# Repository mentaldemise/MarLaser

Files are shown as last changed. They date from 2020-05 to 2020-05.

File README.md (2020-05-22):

https://github.com/adam-p/markdown-here/wiki/Markdown-Cheatsheet#hr

# Making the K40 not suck, a simple plan.

## WARNINGS:
1. This is not going to go into modifying a RAMPS board to support 24V. 
   * If you're brave enough to try this, then use this [link](https://github.com/ExplodingLemur/presentations/wiki/K40-RAMPS-Conversion) to follow his instructions on modifying the board
2. An ability to either solder or spare cash to purchase parts.

# Baseline

This is a Marlin 2.0 build with all the normal laser options set. This is the same firmware configuration that's used in the top "Result" video. The switch from this to that was Lightburn adding support for Inline mode. A Regular Expression can be run on existing Lightburn output as follows:

* Export your gcode for Marlin to desktop. Open it in Notepad++ then:
  * replace all M03 with “I”
  * replace ^(I.+)[\n](G1.+)$ with $2 $1

^This is very much at your own peril. It works for me. I don't mind breaking my stuff.

<a href="https://www.youtube.com/watch?feature=player_embedded&v=LqSpBpukYX4" target="_blank">
IMAGE ALT TEXT HERE
</a>

# Results for just ramps, no stepper upgrade:
<a href="https://www.youtube.com/watch?feature=player_embedded&v=vAA65vcwuIo" target="_blank">
IMAGE ALT TEXT HERE
</a>

## Materials:

### Note on Materials: The initial write-up here is going to be just for RAMPS, then I'm going to add the stuff for my enclosure for exhaust/cooling/air assist, and then come back and add an addendum for using the LPC1768 board for Raster.

* RAMPS 1.4(Trigorilla or other **24V friendly**) *** MKS Board Sgen L V1
* K40 Breakout or skills 
  * https://oshpark.com/shared_projects/3W1BpcNl 
  * $15USD at https://awesome.tech/product/k40-middlemen-board/
  * BRD and SCH files included below for slim version
  * Connector part is linked from [this](https://github.com/ExplodingLemur/presentations/wiki/K40-RAMPS-Conversion) site, search for "connector for the cable"
* 4 Relay board **
* 5V laser diode **
* 3D Printer
* 24V PSU(Or run relay?) **
* 2A stepper for X(At least)

---
Goal: Make K40 not suck.

Inspiration/Source: http://3dprintzothar.blogspot.com/2014/08/40-watt-chinese-co2-laser-upgrade-with.html

## Breakout wiring
#### Note the Buck converter in this picture is used for something else later on.
These are difficult to see, but on my home-made K40 breakout we have:

|Wire Color| Purpose| Pin|
|---|---|---|
|Red| 5V on RAMPS| Any available 5V|
|Black| GND on Ramps| Any available GND|
|4 Pin Dupont| X stepper|X motor|
|White| X Endstop| X- Signal|
|Grey| Y Endstop| Y- Signal|



Use this link to download the Eagle BRD file [Board File](media/k40_breakout/K40_MiddleMan_002A.brd)  
Use this link to download the Eagle SCH file [Board Schematic](media/k40_beakout/K40_MiddleMan_002A.sch)

## Board mount
I used [This thing](https://www.thingiverse.com/thing:2155376) to mount the Trigorilla board in my case. You can find others that will work for whatever RAMPS variant you have. The inpiration link above I think has one for a regule RAMPS even.



## Wiring RAMPS to Laser PSU
PSU Wiring:
#### Note that you may need to check the pinout on your PSU
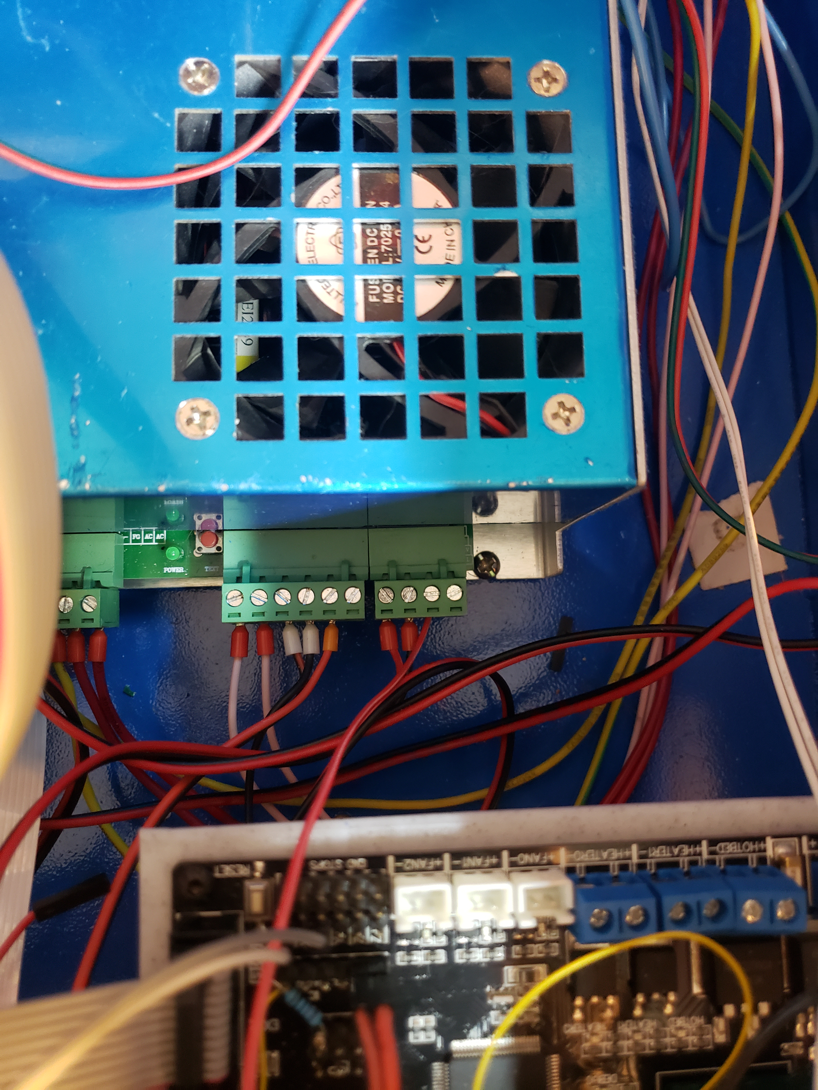
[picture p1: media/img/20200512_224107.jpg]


Top connector(top to bottom)
* NC
* 5V going to any open 5V pin on RAMPS
* GND going to - of 5A input on RAMPS
* +24V going to + of 5A input on RAMPS
---
Bottom Connector(top to bottom)
* NC
* Laser PWM - 6 -- There are only certain pins this can go on because of timers. Leave it on 6 to be safe.
* GND going to any open - on RAMPS
* Laser Enable/Fire - 5 - This is just a digital IO so you can use whichever you want - 10K resistor to +5V here to stop sporadic turnon during boot if interlock is off
* One side of enable push-button toggle
* Other side of enable push-button toggle
---

## Step Calibration
An important part of getting Marlin right on your machine is making sure that distances are correct. If you move 20MM in X when you thought you were going 19MM then there's a bit problem.

This LightBurn file can be used to calibrate steps. There's a 20mmX20mm square with 5mm intervals and axis labels. Cut the outside and etch the inside, measure, and adjust until you get 20x20 with a caliper. Then cut the two triangles(one is rotated 90 degrees), if the two triangles stack up the same then your steps are at least correctly proportioned. 

Use this link to download the Calibration file [Calibration File](media/calibration/20mmSquareStepCal.lbrn)  

~~### 12V buck for Relays
Stepping 24V down to 5V to run switches and the relay coils~~

### Relay board
Runs: Cooling(water pump), Exhaust, and Air Assist via panel buttons

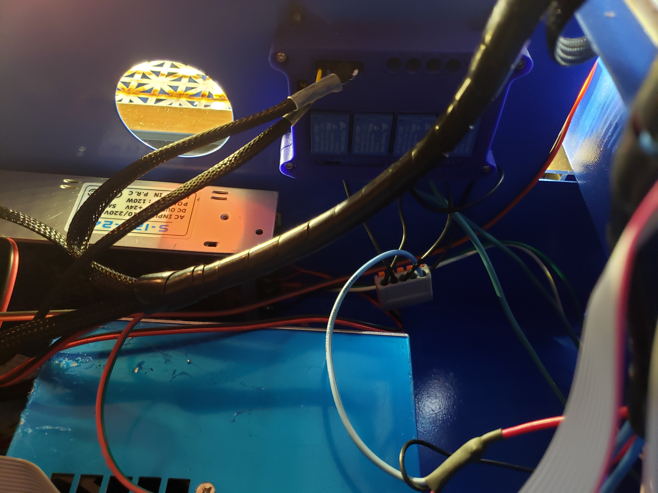
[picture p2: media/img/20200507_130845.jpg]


### Panel

Here's the new panel I have hooked up. The relay board will better explain, but the push buttons are feeding power to a relay in all cases but the aiming diode.

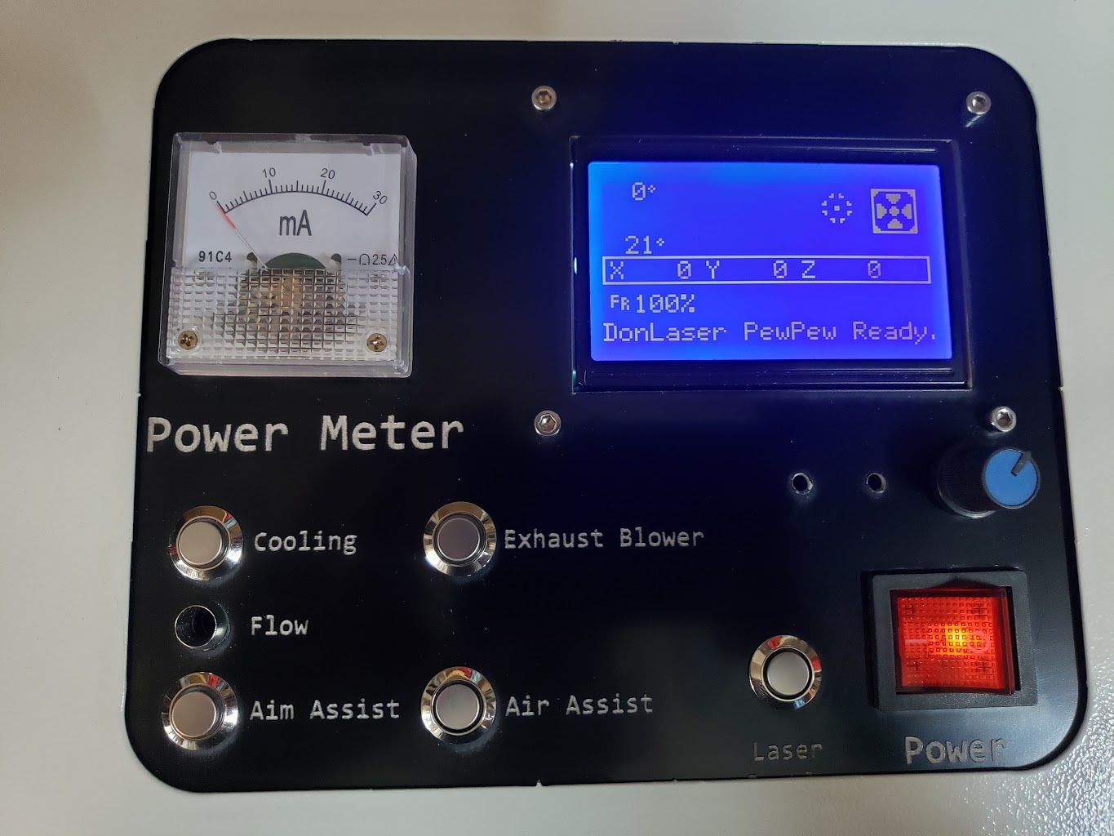
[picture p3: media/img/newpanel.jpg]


Here is the [DXF File](media/panel_files/NewPanel.dxf)
Here is the [LBRN File](media/panel_files/LaserPanel.lbrn)

## Water pump/flow indicator?

*** When hooking up the chiller and cutting my speed/power for MDF went from 10/32 to barely get through to 10/28.

This setup works just fine without the chiller in the loop for the K40 if you turn your pump off between using the laser. I found after a few hours the pump alone would heat the water up(only having 5Gallons doesn't help)

We have an aquarium pump in the bottom of a 5 gallon bucket.  
Outlet on it goes to the IN side of a chiller.  
Outlet of the chiller goes to the IN side of a 12V generator.   
Outlet of the generator then goes to the laser in.

Generator output then goes to the "FLOW" led on the panel. This needs some revision yet.  
There's a Thermistor stuck to the side of the bucket the pump is in and hooked up to TH0 on the RAMPS board to get water temp on the screen as well.

Water pump is controlled via one of the panel buttons and a relay using one of the original outlets on the back of the case(with wiring corrected)

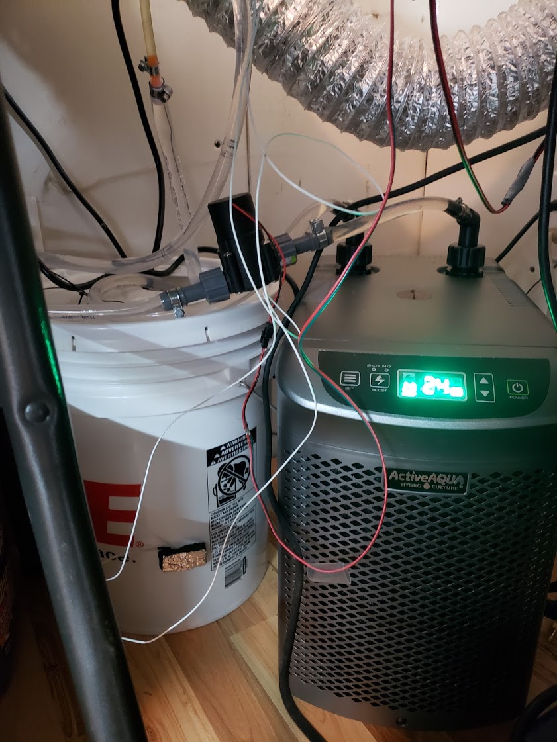
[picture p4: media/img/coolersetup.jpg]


**wire cleanup will come when I get my panel mount connectors this coming week.

## MKS Upgrade for Raster
---
<a href="https://www.youtube.com/watch?feature=player_embedded&v=EFzJmyRZ6YY" target="_blank">
IMAGE ALT TEXT HERE
</a>
---
<a href="https://www.youtube.com/watch?feature=player_embedded&v=5UWSP2m-0Rs" target="_blank">
IMAGE ALT TEXT HERE
</a>

Case was printed using [This thing](https://www.thingiverse.com/thing:4174973) and [this cooling duct](https://www.thingiverse.com/thing:4191051).

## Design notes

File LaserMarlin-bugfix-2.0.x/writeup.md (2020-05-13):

https://github.com/adam-p/markdown-here/wiki/Markdown-Cheatsheet#hr

# Making the K40 not suck, a simple plan.

## Materials:
* RAMPS 1.4(Trigorilla or other 24V friendly preferred) ** MKS Board
* K40 Breakout or skills 
  * https://oshpark.com/shared_projects/3W1BpcNl 
  * $15USD at https://awesome.tech/product/k40-middlemen-board/
* 4 Relay board
* 5V laser diode
* 3D Printer
* 24V PSU(Or run relay?)
* 2A stepper for X(At least)

---
Goal: Make K40 not suck.

Inspiration/Source: http://3dprintzothar.blogspot.com/2014/08/40-watt-chinese-co2-laser-upgrade-with.html

### Breakout wiring

### 12V buck for Relays

### Relay board

### Panel

### Board mount

### Water pump/flow indicator?

## MKS Upgrade for Raster

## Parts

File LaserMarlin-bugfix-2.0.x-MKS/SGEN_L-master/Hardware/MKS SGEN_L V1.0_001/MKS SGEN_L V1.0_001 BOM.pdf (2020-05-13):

Designator | Comment | Footprint | Quantity
AUX-1 | Header 4X2 | DC8P | 1
C1 | 12pF | C0603 | 1
C2 | 12pF | C0603 | 1
C3 | 10uF | C0805 | 1
C4 | 0.1uF | C0603 | 1
C6 | 0.1uF | C0603 | 1
C7 | 0.1uF | C0603 | 1
C8 | 0.1uF | C0603 | 1
C9 | 0.1uF | C0603 | 1
C10 | 0.1uF | C0603 | 1
C11 | 0.1uF | C0603 | 1
C12 | 0.1uF | C0603 | 1
C13 | 100uF | RVT | 1
C14 | 100uF | RVT | 1
C15 | 0.1uF | C0603 | 1
C16 | 0.1uF | C0603 | 1
C17 | 220uF | RVT | 1
C18 | 100uF | RVT | 1
C19 | 0.1uF | C0603 | 1
C20 | 150pF | C0603 | 1
C21 | 10uF | C0805 | 1
C22 | 10uF | C0805 | 1
C23 | 0.1uF | C0603 | 1
C24 | 0.1uF | C0603 | 1
C25 | 0.1uF | C0603 | 1
C26 | 0.1uF | C0603 | 1
C27 | 0.1uF | C0603 | 1
C28 | 0.1uF | C0603 | 1
C29 | 10uF | C0805 | 1
C30 | 10uF | C0805 | 1
C31 | 10uF | C0805 | 1
C32 | 0.1uF | C0603 | 1
C33 | 18pF | C0603 | 1
C34 | 18pF | C0603 | 1
C35 | 0.1uF | C0603 | 1
Cm1_M1 | 100uF | RVT | 1
Cm1_M2 | 100uF | RVT | 1
Cm1_M3 | 100uF | RVT | 1
Cm1_M4 | 100uF | RVT | 1
Cm1_M5 | 100uF | RVT | 1
D1 | LED | LED0603 | 1
D2 | LED | LED0603 | 1
D3 | LED | LED0603 | 1
D4 | LED | LED0603 | 1
D5 | S1G-13-F | D-SMA | 1
D6 | S1A-13-F | D-SMA | 1

D7 | B340A-13-F | D-SMA | 1 D8 | LED | LED0603 | 1 D9 | SS12 | D-SMA | 1 D10 | LED | LED0603 | 1 D11 | LED | LED0603 | 1 D12 | LED | LED0603 | 1 D13 | LED | LED0603 | 1 EXP1 | Header 5X2 | DC10P | 1 EXP2 | Header 5X2 | DC10P | 1 F1 | 30A | F1206 | 1 F2 | 15A | F1206 | 1 F3 | 1A | MF-MSMF050 | 1 F4 | 500mA | MF-MSMF050 | 1 J1 | Header 2 | HDR1X2 | 1 J2 | Header 3X2 | HDR2X3 | 1 J3 | XH-2A | XH-2A | 1 J4 | DG302-4P 5.0 | DG302-5.0-4P | 1 J5 | HG129-2P | HG129-2P | 1 J6 | X- | XH-3A | 1 J7 | X+ | XH-3A | 1 J8 | Y- | XH-3A | 1 J9 | Y+ | XH-3A | 1 J10 | Z- | XH-3A | 1 J11 | Z+ | XH-3A | 1 J12 | Header 5X2 | HDR2X5 | 1 J13 | Header 2 | HDR1X2 | 1 J14 | Header 2 | HDR1X2 | 1 J15 | Header 2 | HDR1X2 | 1 J16 | Header 2 | HDR1X2 | 1 J17 | Header 2 | HDR1X2 | 1 J18 | USB | USBB | 1 J19_M1 | Header 2 | HDR1X2 | 1 J19_M2 | Header 2 | HDR1X2 | 1 J19_M3 | Header 2 | HDR1X2 | 1 J19_M4 | Header 2 | HDR1X2 | 1 J19_M5 | Header 2 | HDR1X2 | 1 J20 | Header 3X2 | HDR2X3 | 1 J21 | XH-2A | XH-2A | 1 J22 | Header 3 | HDR1X3 | 1 Jc1_M1 | Header 4 | HDR1X4 | 1 Jc1_M2 | Header 4 | HDR1X4 | 1 Jc1_M3 | Header 4 | HDR1X4 | 1 Jc1_M4 | Header 4 | HDR1X4 | 1 Jc1_M5 | Header 4 | HDR1X4 | 1 Jm3_M1 | DIP16 | DIP8825 | 1 Jm3_M2 | DIP16 | DIP8825 | 1 Jm3_M3 | DIP16 | DIP8825 | 1

Jm3_M4 | DIP16 | DIP8825 | 1 Jm3_M5 | DIP16 | DIP8825 | 1 Jm4_M1 | Header 4 | HDR1X4 | 1 Jm4_M2 | Header 4 | HDR1X4 | 1 Jm4_M3 | Header 4 | HDR1X4 | 1 Jm4_M4 | Header 4 | HDR1X4 | 1 Jm4_M5 | Header 4 | HDR1X4 | 1 JM1_M1 | Header 4H | XH-4A | 1 JM1_M2 | Header 4H | XH-4A | 1 JM1_M3 | Header 4H | XH-4A | 1 JM1_M4 | Header 4H | XH-4A | 1 JM1_M5 | Header 4H | XH-4A | 1 Jm2_M1 | Header 4X2 | HDR2X4 | 1 Jm2_M2 | Header 4X2 | HDR2X4 | 1 Jm2_M3 | Header 4X2 | HDR2X4 | 1 Jm2_M4 | Header 4X2 | HDR2X4 | 1 Jm2_M5 | Header 4X2 | HDR2X4 | 1 L1 | 15uH/3A | L7*7*4 | 1 LG1 | BLM21 | R0805 | 1 POWER1 | 129-5.08 | 129-5.08 | 1 Q1 | HY1403 | TO-252AA | 1 Q2 | HY1403 | TO-252AA | 1 Q3 | HY1403 | TO-252AA | 1 Q4 | HY3403 | TO-252AA | 1 Q5 | FDN340P | SOT-23 | 1 R1 | 1M | R0603 | 1 R6 | 10K | R0603 | 1 R7 | 10K | R0603 | 1 R8 | 1.8K | R0603 | 1 R9 | 100K | R0603 | 1 R10 | 210k | R0603 | 1 R11 | 40.2k | R0603 | 1 R12 | 24.9k | R0603 | 1 R13 | 100K | R0603 | 1 R14 | 100K | R0603 | 1 R15 | 1K | R0603 | 1 R16 | 1K | R0603 | 1 R17 | 1K | R0603 | 1 R18 | 1K | R0603 | 1 R19 | 1K | R0603 | 1 R20 | 10K | R0603 | 1 R21 | 10K | R0603 | 1 R22 | 10K | R0603 | 1 R23 | 1K | R0603 | 1 R24 | 1K | R0603 | 1 R25 | 1K | R0603 | 1 R26 | 10K | R0603 | 1

R27 | 10K | R0603 | 1 R28 | 10K | R0603 | 1 R29 | 1K | R0603 | 1 R30 | 1K | R0603 | 1 R31 | 1K | R0603 | 1 R32 | 1.5K | R0603 | 1 R33 | 33 | R0603 | 1 R34 | 33 | R0603 | 1 R35 | 33 | R0603 | 1 R37 | 100 | R0603 | 1 R38 | 100 | R0603 | 1 R39 | 10K | R0603 | 1 Rm1_M1 | 10K | R0603 | 1 Rm1_M2 | 10K | R0603 | 1 Rm1_M3 | 10K | R0603 | 1 Rm1_M4 | 10K | R0603 | 1 Rm1_M5 | 10K | R0603 | 1 RPK0 | 1K | RPACK4 | 1 RPK1 | 100 | RPACK4 | 1 RPK2 | 100 | RPACK4 | 1 RPK3 | 100 | RPACK4 | 1 RPK4 | 100 | RPACK4 | 1 RPK5 | 100 | RPACK4 | 1 RPK6 | 100 | RPACK4 | 1 RPK7 | 4.7K | RPACK4 | 1 RPK8 | 100 | RPACK4 | 1 RPK9 | 10K | RPACK4 | 1 RPK10 | 10 | RPACK4 | 1 RPK11 | 100K | RPACK4 | 1 RPK12 | 1.8K | RPACK4 | 1 S1 | TS42 | TS42 | 1 SD | microSD | microSD-2 | 1 TB | Header 2 | XH-2A | 1 TH1 | Header 2 | XH-2A | 1 TH2 | Header 2 | XH-2A | 1 U1 | LPC1768 | LQFP100 | 1 U2 | MP1584 | SOIC8E | 1 U3 | LM1117-3.3V | SOT223-4N | 1 U4 | 74HC125PW | TSSOP-14 | 1 Y1 | 12MHz | CRY5032 | 1 Z1 | CG0603MLC-05E | R0603 | 1 Z2 | CG0603MLC-05E | R0603 | 1 Z3 | CG0603MLC-05E | R0603 | 1

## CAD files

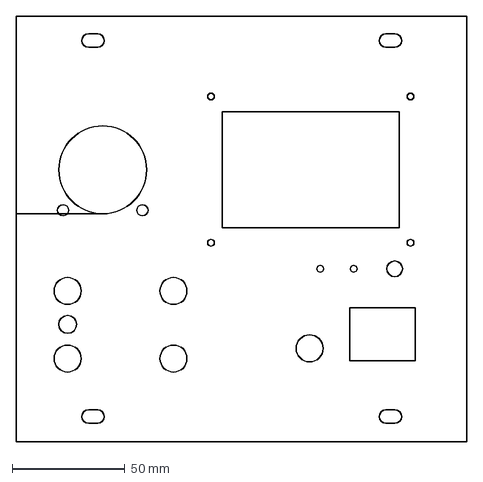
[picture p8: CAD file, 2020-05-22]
media/panel_files/NewPanel.dxf
200.0 x 189.0 mm

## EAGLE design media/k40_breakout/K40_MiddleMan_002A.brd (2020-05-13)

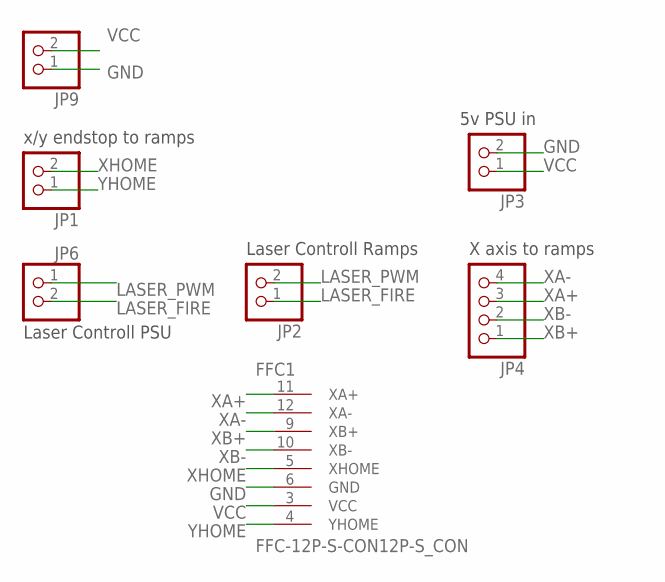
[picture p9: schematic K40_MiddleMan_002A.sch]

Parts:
FFC1: FFC-12P-S-CON12P-S_CON; FFC
JP1, JP2, JP3, JP6, JP9: PINHD-1X2; 1X02
JP4: PINHD-1X4; 1X04

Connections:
GND: FFC1.6 (GND), JP3.2, JP9.1
LASER_FIRE: JP2.1, JP6.2
LASER_PWM: JP2.2, JP6.1
VCC: FFC1.3 (VCC), JP3.1, JP9.2
XA+: FFC1.11 (XA+), JP4.3
XA-: FFC1.12 (XA-), JP4.4
XB+: FFC1.9 (XB+), JP4.1
XB-: FFC1.10 (XB-), JP4.2
XHOME: FFC1.5 (XHOME), JP1.2
YHOME: FFC1.4 (YHOME), JP1.1

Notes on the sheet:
5v PSU in
X axis to ramps
Laser Controll Ramps
Laser Controll PSU
x/y endstop to ramps

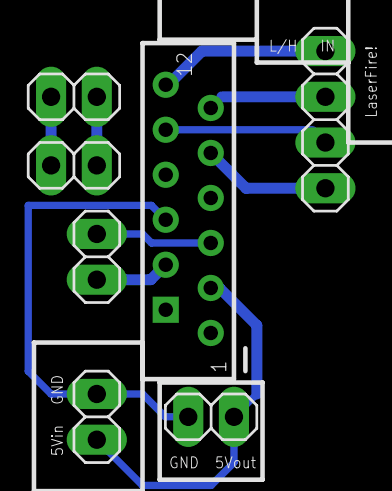
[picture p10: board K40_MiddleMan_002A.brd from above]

Board: 2 copper layers, 7 parts (0 on the bottom side), 10 nets.

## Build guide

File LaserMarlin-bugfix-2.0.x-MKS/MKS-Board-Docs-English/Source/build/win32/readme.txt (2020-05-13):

The bsdtar binaries in this directory were downloaded from http://gnuwin32.sourceforge.net/packages/libarchive.htm
The curl binaries in this directory were downloaded from http://curl.haxx.se/download.html
The md5sum binaries in this directory were downloaded from http://gnuwin32.sourceforge.net/packages/coreutils.htm
The make binaries in this directory were downloaded from http://gnuwin32.sourceforge.net/packages/make.htm

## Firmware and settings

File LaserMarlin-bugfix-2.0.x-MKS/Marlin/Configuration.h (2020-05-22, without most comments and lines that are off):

#pragma once
#define CONFIGURATION_H_VERSION 020005
#define STRING_CONFIG_H_AUTHOR "(DonLaser Pew Pew)" // Who made the changes.
#define SHOW_BOOTSCREEN
#define SERIAL_PORT -1
#define BAUDRATE 250000
  #define MOTHERBOARD BOARD_MKS_SGEN_L
#define CUSTOM_MACHINE_NAME "DonLaser PewPew"
#define EXTRUDERS 1
#define DEFAULT_NOMINAL_FILAMENT_DIA 3.0
#define TEMP_SENSOR_0 1
#define TEMP_SENSOR_1 0
#define TEMP_SENSOR_2 0
#define TEMP_SENSOR_3 0
#define TEMP_SENSOR_4 0
#define TEMP_SENSOR_5 0
#define TEMP_SENSOR_6 0
#define TEMP_SENSOR_7 0
#define TEMP_SENSOR_BED 0
#define TEMP_SENSOR_PROBE 0
#define TEMP_SENSOR_CHAMBER 0
#define DUMMY_THERMISTOR_998_VALUE 25
#define DUMMY_THERMISTOR_999_VALUE 100
#define MAX_REDUNDANT_TEMP_SENSOR_DIFF 10
#define TEMP_RESIDENCY_TIME     10  // (seconds) Time to wait for hotend to "settle" in M109
#define TEMP_WINDOW              1  // (°C) Temperature proximity for the "temperature reached" timer
#define TEMP_HYSTERESIS          3  // (°C) Temperature proximity considered "close enough" to the target
#define TEMP_BED_RESIDENCY_TIME 10  // (seconds) Time to wait for bed to "settle" in M190
#define TEMP_BED_WINDOW          1  // (°C) Temperature proximity for the "temperature reached" timer
#define TEMP_BED_HYSTERESIS      3  // (°C) Temperature proximity considered "close enough" to the target
#define HEATER_0_MINTEMP   5
#define HEATER_1_MINTEMP   5
#define HEATER_2_MINTEMP   5
#define HEATER_3_MINTEMP   5
#define HEATER_4_MINTEMP   5
#define HEATER_5_MINTEMP   5
#define HEATER_6_MINTEMP   5
#define HEATER_7_MINTEMP   5
#define BED_MINTEMP        5
#define HEATER_0_MAXTEMP 275
#define HEATER_1_MAXTEMP 275
#define HEATER_2_MAXTEMP 275
#define HEATER_3_MAXTEMP 275
#define HEATER_4_MAXTEMP 275
#define HEATER_5_MAXTEMP 275
#define HEATER_6_MAXTEMP 275
#define HEATER_7_MAXTEMP 275
#define BED_MAXTEMP      150
#define BANG_MAX 255     // Limits current to nozzle while in bang-bang mode; 255=full current
#define PID_MAX BANG_MAX // Limits current to nozzle while PID is active (see PID_FUNCTIONAL_RANGE below); 255=full current
#define PID_K1 0.95      // Smoothing factor within any PID loop
#define MAX_BED_POWER 255 // limits duty cycle to bed; 255=full current
#define PREVENT_COLD_EXTRUSION
#define EXTRUDE_MINTEMP 170
#define PREVENT_LENGTHY_EXTRUDE
#define EXTRUDE_MAXLENGTH 200
#define USE_XMIN_PLUG
#define USE_YMIN_PLUG
#define USE_ZMIN_PLUG
#define ENDSTOPPULLUPS
#define X_MIN_ENDSTOP_INVERTING false // Set to true to invert the logic of the endstop.
#define Y_MIN_ENDSTOP_INVERTING false // Set to true to invert the logic of the endstop.
#define Z_MIN_ENDSTOP_INVERTING false // Set to true to invert the logic of the endstop.
#define X_MAX_ENDSTOP_INVERTING false // Set to true to invert the logic of the endstop.
#define Y_MAX_ENDSTOP_INVERTING false // Set to true to invert the logic of the endstop.
#define Z_MAX_ENDSTOP_INVERTING false // Set to true to invert the logic of the endstop.
#define Z_MIN_PROBE_ENDSTOP_INVERTING false // Set to true to invert the logic of the probe.
#define X_DRIVER_TYPE  TMC2209
#define Y_DRIVER_TYPE  TMC2209
#define DEFAULT_AXIS_STEPS_PER_UNIT   { 79.25, 79.25, 4000, 500 }
#define DEFAULT_MAX_FEEDRATE          { 3000, 3000, 5, 25 }
#define DEFAULT_MAX_ACCELERATION      { 3000, 3000, 100, 10000 }
#define DEFAULT_ACCELERATION          3000    // X, Y, Z and E acceleration for printing moves
#define DEFAULT_RETRACT_ACCELERATION  3000    // E acceleration for retracts
#define DEFAULT_TRAVEL_ACCELERATION   3000    // X, Y, Z acceleration for travel (non printing) moves
#define CLASSIC_JERK
  #define DEFAULT_XJERK 20.0
  #define DEFAULT_YJERK 20.0
  #define DEFAULT_ZJERK  0.3
  #define LIMITED_JERK_EDITING        // Limit edit via M205 or LCD to DEFAULT_aJERK * 2
    #define MAX_JERK_EDIT_VALUES { 100, 100, 100, 10 } // ...or, set your own edit limits
#define DEFAULT_EJERK    5.0  // May be used by Linear Advance
#define S_CURVE_ACCELERATION
#define Z_MIN_PROBE_USES_Z_MIN_ENDSTOP_PIN
#define NOZZLE_TO_PROBE_OFFSET { 10, 10, 0 }
#define MIN_PROBE_EDGE 10
#define XY_PROBE_SPEED 8000
#define Z_PROBE_SPEED_FAST HOMING_FEEDRATE_Z
#define Z_PROBE_SPEED_SLOW (Z_PROBE_SPEED_FAST / 2)
#define Z_CLEARANCE_DEPLOY_PROBE   10 // Z Clearance for Deploy/Stow
#define Z_CLEARANCE_BETWEEN_PROBES  5 // Z Clearance between probe points
#define Z_CLEARANCE_MULTI_PROBE     5 // Z Clearance between multiple probes
#define Z_PROBE_LOW_POINT          -2 // Farthest distance below the trigger-point to go before stopping
#define Z_PROBE_OFFSET_RANGE_MIN -20
#define Z_PROBE_OFFSET_RANGE_MAX 20
#define X_ENABLE_ON 0
#define Y_ENABLE_ON 0
#define Z_ENABLE_ON 0
#define E_ENABLE_ON 0 // For all extruders
#define DISABLE_X false
#define DISABLE_Y false
#define DISABLE_Z false
#define DISABLE_E false             // For all extruders
#define DISABLE_INACTIVE_EXTRUDER   // Keep only the active extruder enabled
#define INVERT_X_DIR false
#define INVERT_Y_DIR false
#define INVERT_Z_DIR false
#define INVERT_E0_DIR false
#define INVERT_E1_DIR false
#define INVERT_E2_DIR false
#define INVERT_E3_DIR false
#define INVERT_E4_DIR false
#define INVERT_E5_DIR false
#define INVERT_E6_DIR false
#define INVERT_E7_DIR false
#define X_HOME_DIR -1
#define Y_HOME_DIR -1
#define Z_HOME_DIR -1
#define X_BED_SIZE 350
#define Y_BED_SIZE 240
#define X_MIN_POS 0
#define Y_MIN_POS 0
#define Z_MIN_POS 0
#define X_MAX_POS X_BED_SIZE
#define Y_MAX_POS Y_BED_SIZE
#define Z_MAX_POS 200
#define MIN_SOFTWARE_ENDSTOPS
  #define MIN_SOFTWARE_ENDSTOP_X
  #define MIN_SOFTWARE_ENDSTOP_Y
  #define MIN_SOFTWARE_ENDSTOP_Z
#define MAX_SOFTWARE_ENDSTOPS
  #define MAX_SOFTWARE_ENDSTOP_X
  #define MAX_SOFTWARE_ENDSTOP_Y
  #define MAX_SOFTWARE_ENDSTOP_Z
#define HOMING_FEEDRATE_XY (50*60)
#define HOMING_FEEDRATE_Z  (4*60)
#define VALIDATE_HOMING_ENDSTOPS
#define EEPROM_SETTINGS     // Persistent storage with M500 and M501
#define EEPROM_CHITCHAT       // Give feedback on EEPROM commands. Disable to save PROGMEM.
#define EEPROM_BOOT_SILENT    // Keep M503 quiet and only give errors during first load
  #define EEPROM_AUTO_INIT  // Init EEPROM automatically on any errors.
#define DEFAULT_KEEPALIVE_INTERVAL 2  // Number of seconds between "busy" messages. Set with M113.
#define BUSY_WHILE_HEATING            // Some hosts require "busy" messages even during heating
#define PREHEAT_1_LABEL       "PLA"
#define PREHEAT_1_TEMP_HOTEND 180
#define PREHEAT_1_TEMP_BED     70
#define PREHEAT_1_FAN_SPEED     0 // Value from 0 to 255
#define PREHEAT_2_LABEL       "ABS"
#define PREHEAT_2_TEMP_HOTEND 240
#define PREHEAT_2_TEMP_BED    110
#define PREHEAT_2_FAN_SPEED     0 // Value from 0 to 255
#define PRINTJOB_TIMER_AUTOSTART
#define LCD_LANGUAGE en
#define DISPLAY_CHARSET_HD44780 JAPANESE
#define LCD_INFO_SCREEN_STYLE 0
#define INDIVIDUAL_AXIS_HOMING_MENU
#define REPRAP_DISCOUNT_FULL_GRAPHIC_SMART_CONTROLLER
#define SOFT_PWM_SCALE 0
#define SERVO_DELAY { 0 }

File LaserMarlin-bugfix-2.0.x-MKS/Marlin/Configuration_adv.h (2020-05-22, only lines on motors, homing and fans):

#define E0_AUTO_FAN_PIN -1
#define E1_AUTO_FAN_PIN -1
#define E2_AUTO_FAN_PIN -1
#define E3_AUTO_FAN_PIN -1
#define E4_AUTO_FAN_PIN -1
#define E5_AUTO_FAN_PIN -1
#define E6_AUTO_FAN_PIN -1
#define E7_AUTO_FAN_PIN -1
#define CHAMBER_AUTO_FAN_PIN -1
#define HOMING_BUMP_MM      { 5, 5, 2 }       // (mm) Backoff from endstops after first bump
#define HOMING_BUMP_DIVISOR { 2, 2, 4 }       // Re-Bump Speed Divisor (Divides the Homing Feedrate)
#define QUICK_HOME                          // If G28 contains XY do a diagonal move first
#define HOME_AFTER_DEACTIVATE  // Require rehoming after steppers are deactivated
#define MICROSTEP_MODES { 16, 16, 16, 16, 16, 16 } // [1,2,4,8,16]
    #define X_CURRENT       1500        // (mA) RMS current. Multiply by 1.414 for peak current.
    #define X_CURRENT_HOME  X_CURRENT  // (mA) RMS current for sensorless homing
    #define X_MICROSTEPS     16    // 0..256
    #define Y_CURRENT       1300
    #define Y_CURRENT_HOME  Y_CURRENT
    #define Y_MICROSTEPS     16
  #define X_HYBRID_THRESHOLD     100  // [mm/s]
  #define X2_HYBRID_THRESHOLD    100
  #define Y_HYBRID_THRESHOLD     100
  #define Y2_HYBRID_THRESHOLD    100
  #define Z_HYBRID_THRESHOLD       3
  #define Z2_HYBRID_THRESHOLD      3
  #define Z3_HYBRID_THRESHOLD      3
  #define Z4_HYBRID_THRESHOLD      3
  #define E0_HYBRID_THRESHOLD     30
  #define E1_HYBRID_THRESHOLD     30
  #define E2_HYBRID_THRESHOLD     30
  #define E3_HYBRID_THRESHOLD     30
  #define E4_HYBRID_THRESHOLD     30
  #define E5_HYBRID_THRESHOLD     30
  #define E6_HYBRID_THRESHOLD     30
  #define E7_HYBRID_THRESHOLD     30

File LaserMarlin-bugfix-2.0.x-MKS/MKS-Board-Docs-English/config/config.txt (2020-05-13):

# NOTE Lines must not exceed 132 characters
# Robot module configurations : general handling of movement G-codes and slicing into moves
default_feed_rate                            4000             # Default rate ( mm/minute ) for G1/G2/G3 moves
default_seek_rate                            4000             # Default rate ( mm/minute ) for G0 moves
mm_per_arc_segment                           0.5              # Arcs are cut into segments ( lines ), this is the length for
                                                              # these segments.  Smaller values mean more resolution,
                                                              # higher values mean faster computation
mm_per_line_segment                          5                # Lines can be cut into segments ( not usefull with cartesian
                                                              # coordinates robots ).

# Arm solution configuration : Cartesian robot. Translates mm positions into stepper positions
alpha_steps_per_mm                           78.7402               # Steps per mm for alpha stepper
beta_steps_per_mm                            78.7402               # Steps per mm for beta stepper
gamma_steps_per_mm                           400             # Steps per mm for gamma stepper

# Planner module configuration : Look-ahead and acceleration configuration
planner_queue_size                           32               # DO NOT CHANGE THIS UNLESS YOU KNOW EXACTLY WHAT YOU ARE DOING
acceleration                                 600             # Acceleration in mm/second/second.
z_acceleration                              60              # Acceleration for Z only moves in mm/s^2, 0 uses acceleration which is the default. DO NOT SET ON A DELTA
acceleration_ticks_per_second                1000             # Number of times per second the speed is updated
junction_deviation                           0.02             # Similar to the old "max_jerk", in millimeters,
                                                              # see https://github.com/grbl/grbl/blob/master/planner.c
                                                              # and https://github.com/grbl/grbl/wiki/Configuring-Grbl-v0.8
                                                              # Lower values mean being more careful, higher values means being
                                                              # faster and have more jerk
#z_junction_deviation                        0.0              # for Z only moves, -1 uses junction_deviation, zero disables junction_deviation on z moves DO NOT SET ON A DELTA
#minimum_planner_speed                       0.0              # sets the minimum planner speed in mm/sec





# Stepper module configuration
microseconds_per_step_pulse                  1                # Duration of step pulses to stepper drivers, in microseconds
base_stepping_frequency                      100000           # Base frequency for stepping, higher gives smoother movement

# Cartesian axis speed limits
x_axis_max_speed                             10000            # mm/min
y_axis_max_speed                             10000            # mm/min
z_axis_max_speed                             200              # mm/min

# Stepper module pins ( ports, and pin numbers, appending "!" to the number will invert a pin )
alpha_step_pin                               2.0              # Pin for alpha stepper step signal
alpha_dir_pin                                0.5!              # Pin for alpha stepper direction
alpha_en_pin                                 0.4              # Pin for alpha enable pin
alpha_max_rate                               10000.0          # mm/min

beta_step_pin                                2.1              # Pin for beta stepper step signal
beta_dir_pin                                 0.11             # Pin for beta stepper direction
beta_en_pin                                  0.10             # Pin for beta enable
beta_max_rate                                10000.0          # mm/min

gamma_step_pin                               2.2              # Pin for gamma stepper step signal
gamma_dir_pin                                0.20!             # Pin for gamma stepper direction
gamma_en_pin                                 0.19             # Pin for gamma enable
gamma_max_rate                               100.0            # mm/min

# Serial communications configuration ( baud rate default to 9600 if undefined )
uart0.baud_rate                              115200           # Baud rate for the default hardware serial port
second_usb_serial_enable                     true            # This enables a second usb serial port (to have both pronterface
                                                              # and a terminal connected)
#leds_disable                                true             # disable using leds after config loaded
#play_led_disable                            true             # disable the play led
pause_button_enable                          true             # Pause button enable
#pause_button_pin                            2.12             # pause button pin. default is P2.12
#kill_button_enable                           false            # set to true to enable a kill button
#kill_button_pin                              2.12             # kill button pin. default is same as pause button 2.12 (2.11 is another good choice)
#msd_disable                                 false            # disable the MSD (USB SDCARD) when set to true (needs special binary)
#dfu_enable                                  false            # for linux developers, set to true to enable DFU

# Extruder module configuration
extruder.hotend.enable                          true             # Whether to activate the extruder module at all. All configuration is ignored if false
extruder.hotend.steps_per_mm                    90              # Steps per mm for extruder stepper
extruder.hotend.default_feed_rate               600              # Default rate ( mm/minute ) for moves where only the extruder moves
extruder.hotend.acceleration                    500              # Acceleration for the stepper motor, as of 0.6, arbitrary ratio
extruder.hotend.max_speed                       50               # mm/s

extruder.hotend.step_pin                        2.3              # Pin for extruder step signal
extruder.hotend.dir_pin                         0.22!             # Pin for extruder dir signal
extruder.hotend.en_pin                          0.21             # Pin for extruder enable signal

# extruder offset
#extruder.hotend.x_offset                        0                # x offset from origin in mm
#extruder.hotend.y_offset                        0                # y offset from origin in mm
#extruder.hotend.z_offset                        0                # z offset from origin in mm

# firmware retract settings when using G10/G11, these are the defaults if not defined, must be defined for each extruder if not using the defaults
#extruder.hotend.retract_length                  3               # retract length in mm
#extruder.hotend.retract_feedrate                45              # retract feedrate in mm/sec
#extruder.hotend.retract_recover_length          0               # additional length for recover
#extruder.hotend.retract_recover_feedrate        8               # recover feedrate in mm/sec (should be less than retract feedrate)
#extruder.hotend.retract_zlift_length            0               # zlift on retract in mm, 0 disables
#extruder.hotend.retract_zlift_feedrate          6000            # zlift feedrate in mm/min (Note mm/min NOT mm/sec)



# Second extruder module configuration
#extruder.hotend2.enable                          true             # Whether to activate the extruder module at all. All configuration is ignored if false
#extruder.hotend2.steps_per_mm                    140              # Steps per mm for extruder stepper
#extruder.hotend2.default_feed_rate               600              # Default rate ( mm/minute ) for moves where only the extruder moves
#extruder.hotend2.acceleration                    500              # Acceleration for the stepper motor, as of 0.6, arbitrary ratio
#extruder.hotend2.max_speed                       50               # mm/s

#extruder.hotend2.step_pin                        2.8              # Pin for extruder step signal
#extruder.hotend2.dir_pin                         2.13             # Pin for extruder dir signal
#extruder.hotend2.en_pin                          4.29             # Pin for extruder enable signal

#extruder.hotend2.x_offset                        0                # x offset from origin in mm
#extruder.hotend2.y_offset                        25.0             # y offset from origin in mm
#extruder.hotend2.z_offset                        0                # z offset from origin in mm
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

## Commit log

2020-05-13 Moving from BitBucket.
    [Configuration.h, Configuration_adv.h, K40_MiddleMan_002A.brd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]
2020-05-14 Adjusting steps on X asix for swapped in new stepper, also adjusting Y after calibration test. LB file included, use the square until you get 20 on each then verify with the two triangles.
    [Configuration.h]
2020-05-14 Adding step calibration to readme.
2020-05-15 Fixing steps and setting current to more reasonable values. :D EEPROM is still an issue, may need to merge in latest changes.
    [Configuration.h, Configuration_adv.h]
2020-05-15 Latest MKS setting tweaks. No idea what I'm doing. Trying to slam the head back and forth faster with the 2A stepper.
    [Configuration.h]
2020-05-16 About to pull changes and turn off TMC stuff to save CPU cycles.
    [Configuration_adv.h]
2020-05-16 Turning off TMC stuff to save CPU cycles.
    [Configuration_adv.h]
2020-05-22 Adding messed up panel with upside down ammeter like original
    [NewPanel.dxf]
2020-05-22 Setting changes for swapped in Y motor(1.8A with dual shaft)
    [Configuration.h, Configuration_adv.h]
2020-05-22 better version but "Enable" was noticed to be seen missing(hidden under bezel)
    [NewPanel.dxf]

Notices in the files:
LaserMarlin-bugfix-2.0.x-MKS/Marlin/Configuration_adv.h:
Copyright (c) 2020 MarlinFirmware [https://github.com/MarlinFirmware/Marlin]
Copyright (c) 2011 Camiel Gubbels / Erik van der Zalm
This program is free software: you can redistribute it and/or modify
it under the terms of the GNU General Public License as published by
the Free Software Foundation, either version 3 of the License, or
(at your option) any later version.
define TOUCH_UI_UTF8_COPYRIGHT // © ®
